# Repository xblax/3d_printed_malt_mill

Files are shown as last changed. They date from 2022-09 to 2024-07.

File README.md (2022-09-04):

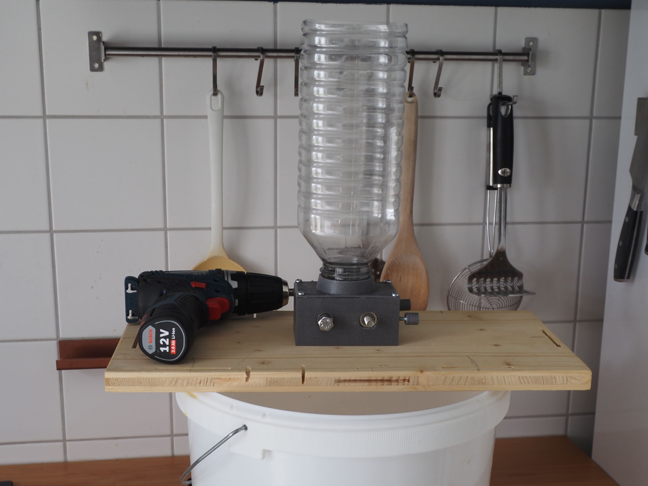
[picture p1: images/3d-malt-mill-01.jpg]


# 3D Printed Malt Mill

This is an open source malt mill design intended mainly for homebrewers with ~20 l batches and ~5 kg grain bills. The mill was designed to only use parts that are  available in many hardware stores to allow easy DIY reproduction and to keep the overall cost low.

For now, this design should still be considered as a work in progress - there is no long term experience for it's durability yet. To get a first impression you can check the photos in the [images](images) folder.

## Main Features

* Geared 40x40 mm rollers with ball bearings
* Adjustable gap (0.25 mm - 2.75 mm gap size)
* Separate hopper attachment part (currently one design for Bericap 48-41 threads)
* Powered by cordless screwdriver

## Bill of materials

Besides food safe PETG or PLA filament you need:

| Pieces | Part | Purpose
| --- | :--- | :---
| 2 | M8 x 80 mm fully threaded hex bolt | Axles
| 5 | M8 hex nut | Roller and gear insert nuts
| 4 | 608 ZZ bearing | Roller bearings
| 2 | M4 hex bolt | Adjustment screws
| 2 | M4 hex nut | Adjustment screw inserts
| 4 | 3x15 mm screws (spax or similiar) | Hopper attachment
| 4-6 | 3 mm screws (20 mm + board thickness) | Board attachment
| 1 | Bericap 48-41 threaded bottle | Hopper

Buying recommendations for Germans:  
All metal parts including the bearings should be cheaply available at Hornbach hardware store.
Bericap 48-41 threaded bottles are sold with 2-5 l distilled water in in many stores (i.e. DM, Edeka -- effective 2022).

## Printing considerations

Parts are intended to be printed with 0.25mm layer hight. The model pictured above was printed with PETG.

| Pieces | Part | File
| --- | :--- | :---
| 1 | Main mill frame | [frame.stl](stl/frame.stl)
| 2 | Roller | [roller.stl](stl/roller.stl)
| 2 | Gear | [gear.stl](stl/gear.stl)
| 2 | Adjustment knob | [knob.stl](stl/knob.stl)
| 1 | Spacer | [spacer.stl](stl/spacer.stl)
| 1 | Hopper attachment | [attachment\_bericap\_4841.stl](stl/attachment_bericap_4841.stl)

It's recommended to print the test parts in [stl/testparts](stl/testparts) first to test fitting of the parts and settings of your 3D printer.

#### Frame
Should be printed upside down. 2 perimeters, 3 top/bottom layers, 12-15% rectilinear infill should be sufficient. No support required.

#### Rollers

Should be printed in direction as rendered. Auto-generated support is required for the bottom nut insert. The lower nut insert is designed a bit deeper than the upper one to counter sagging of the top layers when printing.

Recommended settings are 3 perimeters and 15% rectilinear support. Consider to increase infill, perimeters or to add some solid layers for the first and last 6mm to improve strength of the nut inserts.

#### Gears

Should be printed with flat side down. Auto generated support for nut insert required. 3 perimeters, 3 top/bottom solid layers, 15% rectilinear infill.

## Assembly

All parts are press-fit or screwed together. The mill should be attached to a base board, screwed from the bottom.

## Source Files

Most parts were designed with Open Scad 2021.01. Exception are the gears which were created with FreeCad 0.19.

## License

This project is licensed under GPL v3. 

If you distribute STLs or prints based on this design you are require to provide the (changed) source files along with a copy of the GPL v3 license.

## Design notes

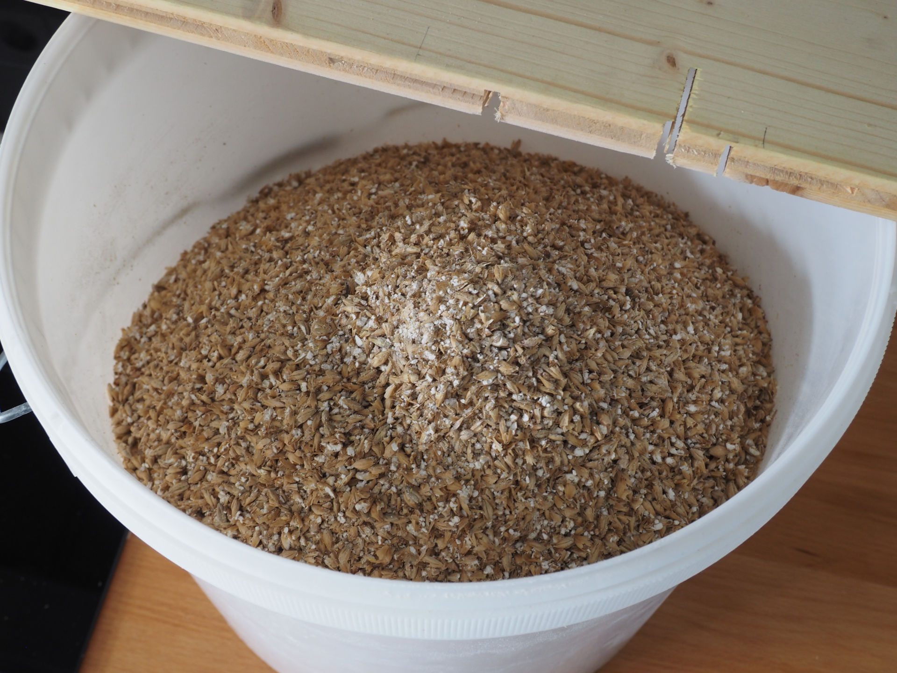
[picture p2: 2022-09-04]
images/3d-malt-mill-03.jpg

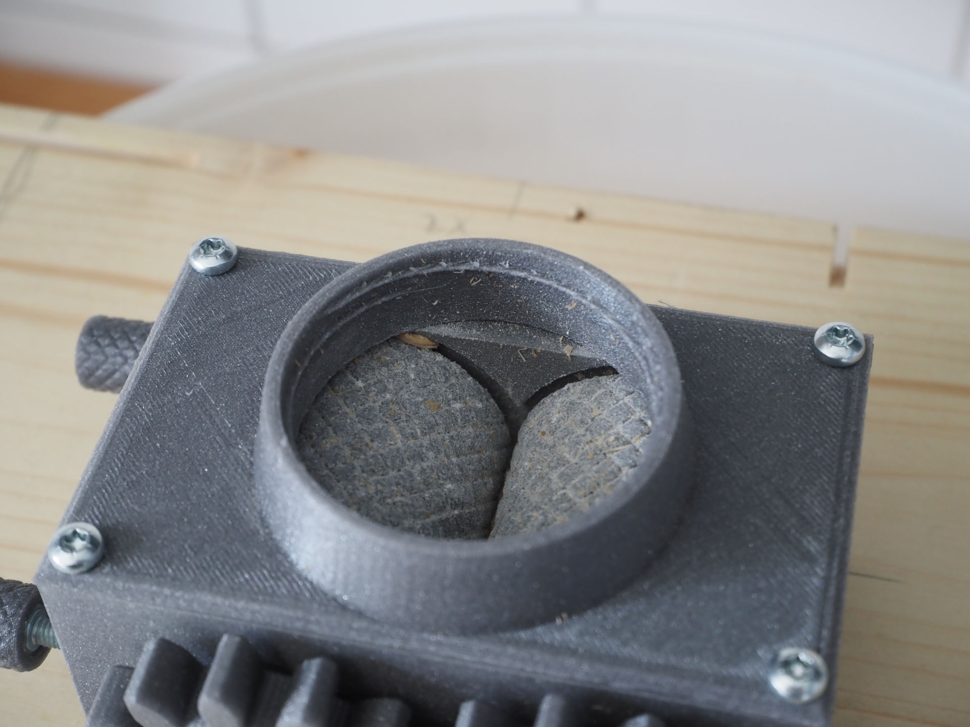
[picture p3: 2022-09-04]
images/3d-malt-mill-02.jpg

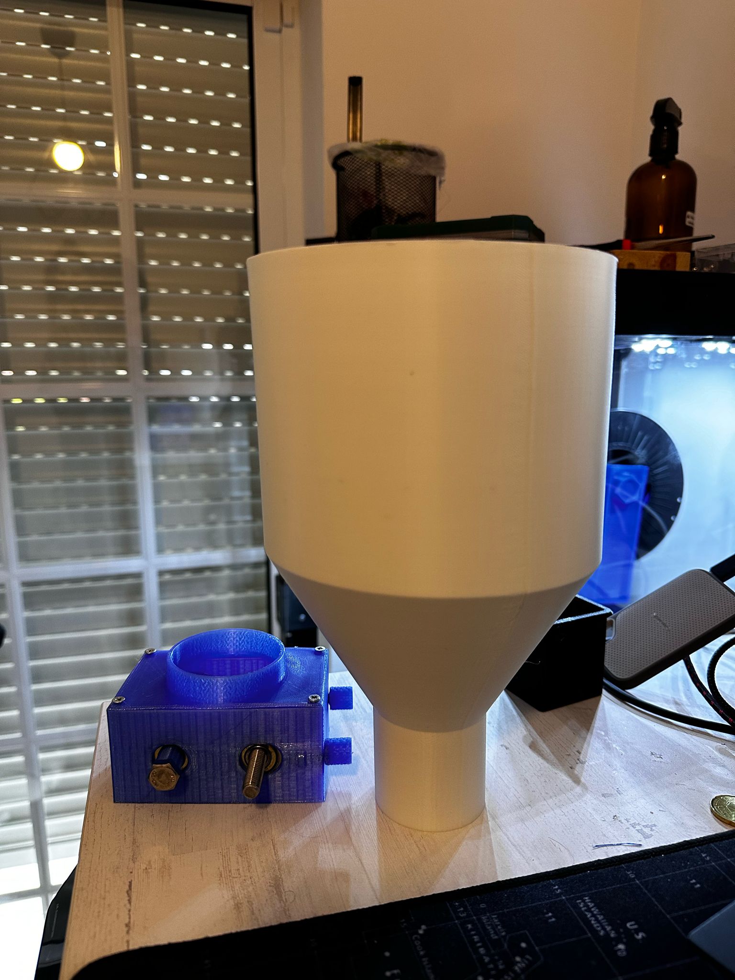
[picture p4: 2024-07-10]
images/funnel and attachment.jpg

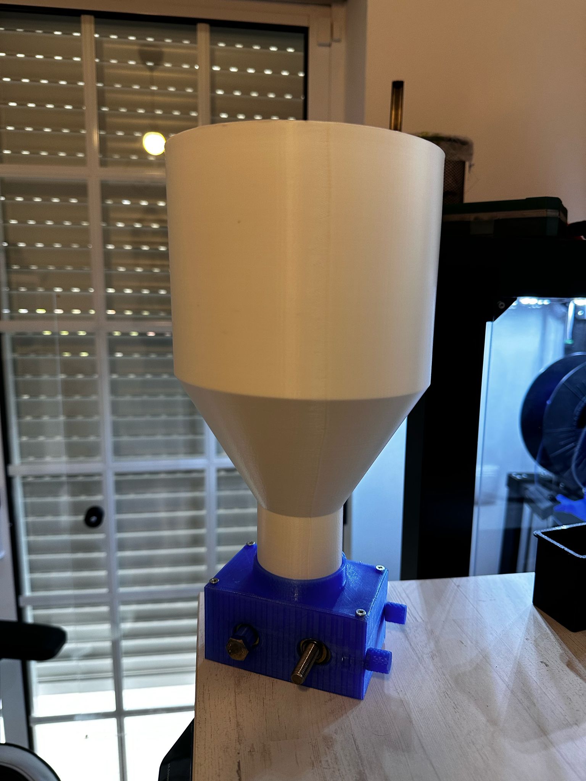
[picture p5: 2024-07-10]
images/funnel and lid.jpg

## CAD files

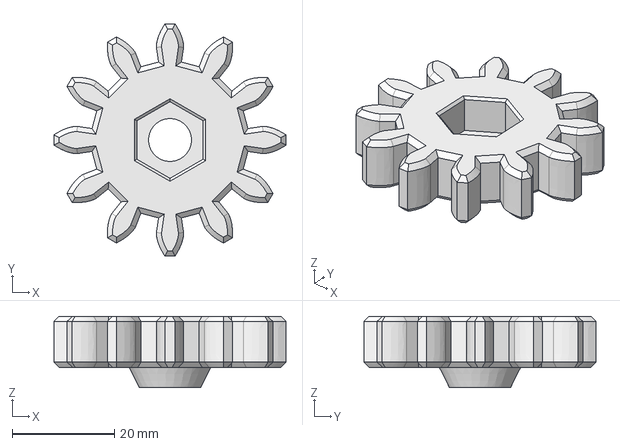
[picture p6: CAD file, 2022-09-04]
src/gear.FCStd
45.5 x 45.5 x 14.0 mm

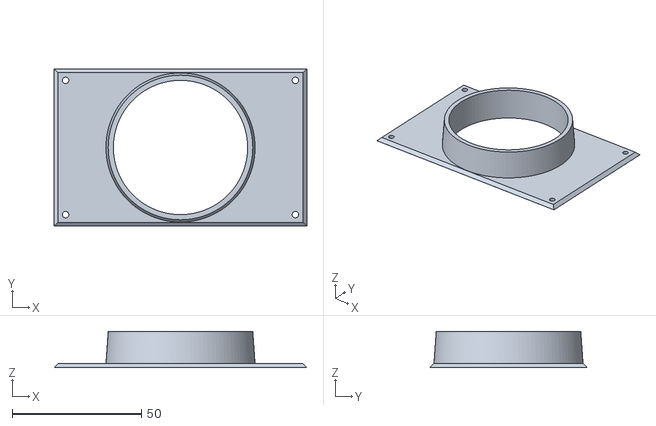
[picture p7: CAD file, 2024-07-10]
stl/attachment_no_thread.stl
98.0 x 61.0 x 14.0

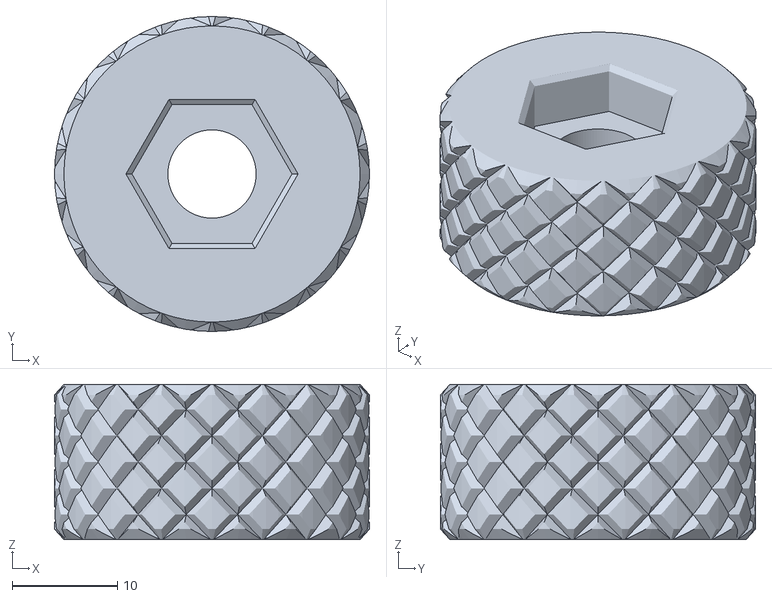
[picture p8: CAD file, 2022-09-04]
stl/testparts/test_roller.stl
30.0 x 30.0 x 14.8

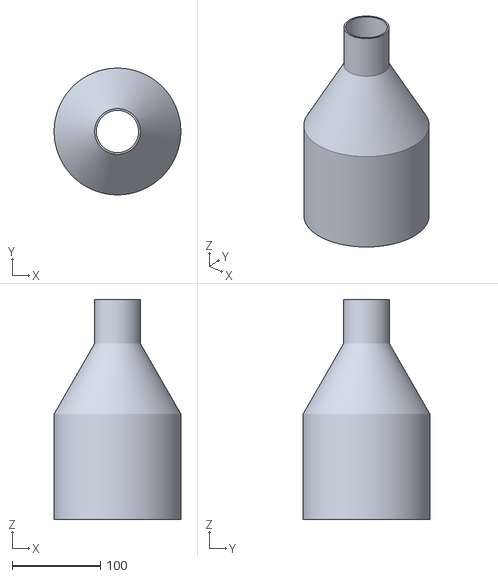
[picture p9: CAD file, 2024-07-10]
stl/funnel_no_thread.stl
144.0 x 144.0 x 250.0

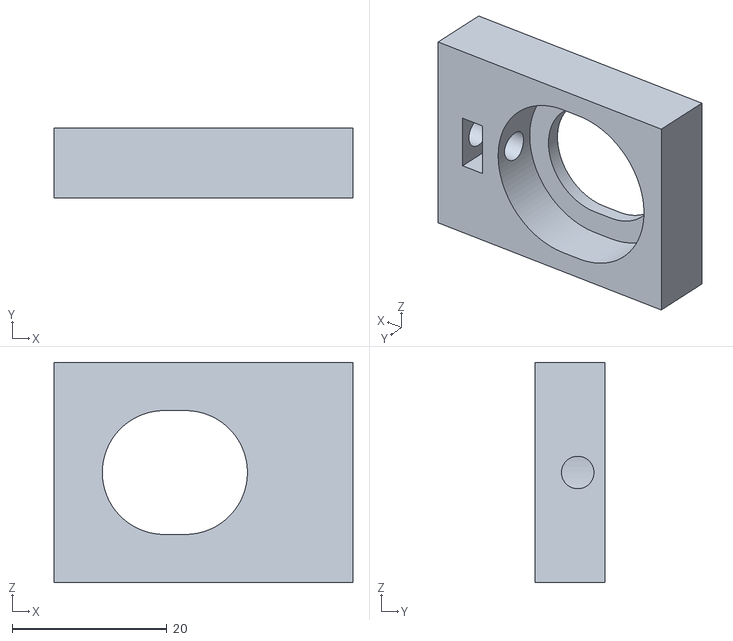
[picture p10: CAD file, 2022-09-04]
stl/testparts/test_frame.stl
38.6 x 9.00 x 28.5

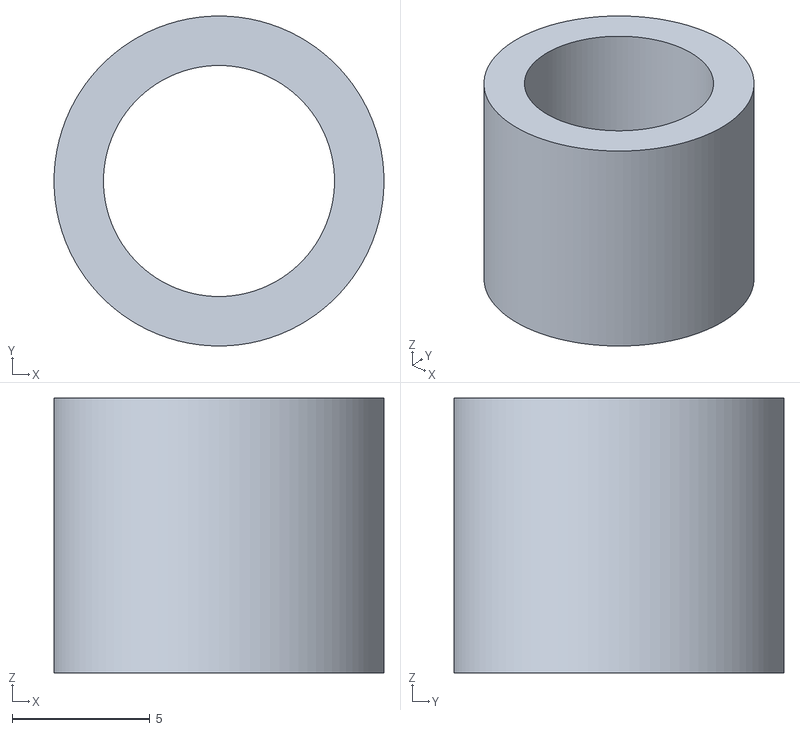
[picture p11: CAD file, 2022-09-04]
stl/spacer.stl
12.0 x 12.0 x 10.0

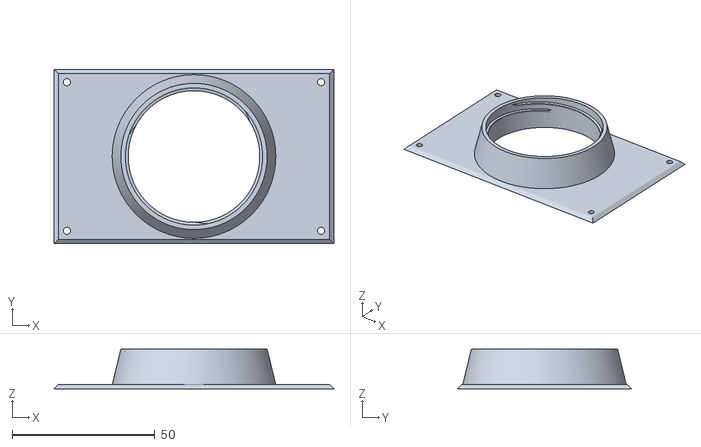
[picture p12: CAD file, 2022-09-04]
stl/attachment_bericap_4841.stl
98.0 x 61.0 x 14.0

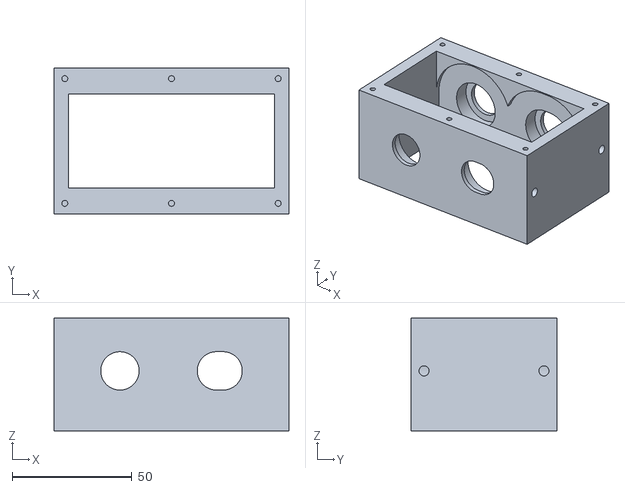
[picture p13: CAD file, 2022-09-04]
stl/frame.stl
98.0 x 61.0 x 47.0

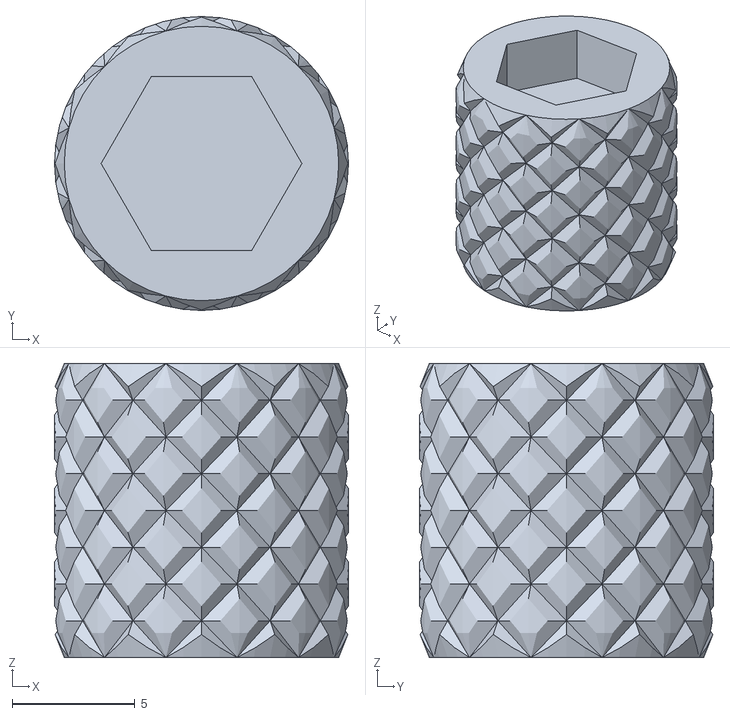
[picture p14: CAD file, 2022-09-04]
stl/knob.stl
12.0 x 12.0 x 12.0

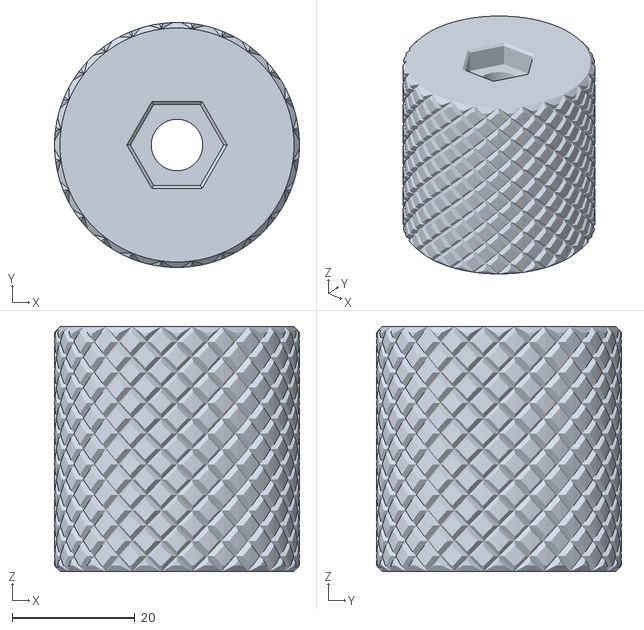
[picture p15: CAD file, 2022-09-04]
stl/roller.stl
40.0 x 40.0 x 40.0

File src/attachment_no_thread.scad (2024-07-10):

/* 
 * 3D Printed Malt Mill
 * Designed by xblax: https://github.com/xblax/3d_printed_malt_mill
 * Licensed GPL v3 
 */

use <knurledFinishLib_v2_1.scad>
use <thread_profile.scad>

$fn=100;
$eps=0.01;

// roller dimensions
$roller_width=40;
$roller_diameter=40;
$roller_min_dist=0.25;   // minimum distance between the two rollers
$roller_adj_range=2.75; // adjustable range of second roller

$roller_side_clearance=1.5;
$roller_head_clearance=1.5;
$roller_top_clearance=1.5;
$roller_bottom_clearance=5; // note: 5mm needed due to gear size

// frame walls
$frame_head_width=9; // thick enough for 7mm bearing inset
$frame_side_width=6;
$frame_top_width=0.5;

// calculated values
$frame_inner_width=$roller_diameter*2+$roller_side_clearance*2+$roller_min_dist+$roller_adj_range;
$frame_inner_depth=$roller_width+$roller_head_clearance*2;
$frame_inner_height=$roller_diameter+$roller_bottom_clearance+$roller_top_clearance;

$frame_width=$frame_inner_width+$frame_side_width*2;
$frame_height=$frame_inner_height+$frame_top_width;
$frame_depth=$frame_inner_depth+$frame_head_width*2;

$primary_roller_x=$frame_side_width+$roller_side_clearance+$roller_diameter/2;
$secondary_roller_x=$frame_side_width+$roller_side_clearance+$roller_diameter/2*3+$roller_min_dist;
$roller_z=$roller_bottom_clearance+$roller_diameter/2;

// mouting holes
$mounting_hole_diameter = 2.5; // to be used with 3mm screws
$mounting_hole_depth = 20; // should not collide with adjusment mechanism
$mounting_hole_inset = $frame_head_width/2;
$attachment_hole_depth = 15;


// top opening of frame
$top_opening_roller_overlap=2;
$top_opening_width=$frame_inner_width;
$top_opening_depth=$frame_inner_depth - 2 * $top_opening_roller_overlap;

// roller knurling
$knurl_wd=5;
$knurl_hg=5;
$knurl_dp=3;
$knurl_e_smooth=1;
$knurl_s_smooth=70;
$knurl_cylinder_od=$roller_diameter-($knurl_dp*(100-$knurl_s_smooth)/100); // calculate cylinder diameter (total diamater minus knurling)

// roller M8 axis parameters
$roller_axis_through_hole=8.4;
$insert_nut_size=13.2;
$insert_nut_thickness=6.25;
$insert_nut_clearance=0.15; // clearance between nuts and bearings - 0.3mm in total
$insert_nut_inset_bottom_adjust=0.5; // bottom side of the roller needs 0.5mm additional inset for the nut to due sagging of top layers when printed with support
$insert_nut_inset=$insert_nut_thickness - $roller_side_clearance + $insert_nut_clearance;
$insert_nut_outset=$insert_nut_thickness - $insert_nut_inset;
$insert_nut_chamfer=0.5;
$square_nut = false;

// paramters for 608Z bearings
$bearing_hole_diameter = 16;
$bearing_inset_depth = 7;
$bearing_inset_diameter = 22.5;

// adjustment mechanism: M4 parameters
$adj_screw_diameter=4.2;
$adj_nut_size=7.5;
$adj_nut_thickness=3.4;
$adj_nut_space=4;

// adjustment mechanism: knob parameters
$knob_height = 12;
$knob_width = 12;
$knob_nut_size=7.1;
$knob_nut_inset=3;

$knob_knurl_wd=3;
$knob_knurl_hg=3;
$knob_knurl_dp=1;
$knob_knurl_e_smooth=1;
$knob_knurl_s_smooth=60;
$knob_knurl_od=$knob_width-($knob_knurl_dp*(100-$knob_knurl_s_smooth)/100);

// attachment plate
$attachment_base_width = $frame_width;
$attachment_base_depth = $frame_depth;
$attachment_base_thickness = 1.5;
$attachment_wall_thickness=1.6;

// test object parameters
$test_roller_diameter=30;
$test_roller_width=$insert_nut_inset*2+5;
$test_knurl_cylinder_od=$test_roller_diameter-($knurl_dp*(100-$knurl_s_smooth)/100);

echo(str("Frame dimensions: ", $frame_width, " x ", $frame_depth, " x ", $frame_height));
echo(str("Cutout dimensions: ", $frame_inner_width, " x ", $frame_inner_depth));
echo(str("Mouting screws: ", ($frame_inner_width+$frame_head_width), " x ", ($frame_inner_depth+$frame_head_width), " (outset from cutout ", $frame_head_width/2, "mm)"));
//echo(str("Roller Distance ", $secondary_roller_x-$primary_roller_x, " + ", $roller_adj_range));
//echo(str("Roller Nut Outset ", $insert_nut_outset));

module nut(size, height)
{
    if( $square_nut )
    {  
        // square nut
        cube([size,size,height],center=true);
    }
    else
    {
        // hex nut
        cylinder($fn=6, d=size/cos(30), h=height, center=true);  
    }
}

module insert_nut_chamfer()
{
    hull()
    {
        translate([0,0,$insert_nut_chamfer])
        nut($insert_nut_size,$eps);
        nut($insert_nut_size+2*$insert_nut_chamfer, $eps);
    }
}

module roller_top_nut_insert(roller_width=$roller_width)
{
    translate([0,0,roller_width-$insert_nut_inset+$insert_nut_thickness/2])
    nut($insert_nut_size,$insert_nut_thickness);
    translate([0,0,roller_width])
    rotate([180,0,0])
    insert_nut_chamfer();
}

module roller_bottom_nut_insert()
{
    translate([0,0,($insert_nut_inset+$insert_nut_inset_bottom_adjust)-$insert_nut_thickness/2])
    nut($insert_nut_size,$insert_nut_thickness);
    insert_nut_chamfer();
}

/* Roller part for the malt mill (required twice) */
module roller()
{
    difference()
    {
        // Knurled cylinder
        knurl(k_cyl_hg= $roller_width, k_cyl_od = $knurl_cylinder_od, knurl_wd=$knurl_wd, knurl_hg=$knurl_hg, knurl_dp=$knurl_dp, e_smooth = $knurl_e_smooth, s_smooth=$knurl_s_smooth);

        // axis trough hole
        translate([0,0,-$eps])
        cylinder(d=$roller_axis_through_hole, h = $roller_width+1, $fn=100);
        // Top nut insert
        roller_top_nut_insert();
        // Bottom nut insert 
        roller_bottom_nut_insert();
    }
}

module base_frame()
{
    difference()
    {
        cube([$frame_width,$frame_depth,$frame_inner_height]);
        translate([$frame_side_width,$frame_head_width,-$eps])
        cube([$frame_inner_width,$frame_inner_depth,$frame_inner_height+2*$eps]);  
    }
}

module axis_through_hole(xpos,zpos=$roller_z)
{
    translate([xpos,-$eps,zpos])
    rotate([-90,0,0])
    cylinder(h=$frame_depth+2*$eps,d=$bearing_hole_diameter);
}

module bearing_cylinder(xpos,zpos=$roller_z)
{
    bearing_cylinder_length=$frame_inner_depth+2*$bearing_inset_depth;
    bearing_cylinder_y=$frame_head_width-$bearing_inset_depth;  
    translate([xpos,bearing_cylinder_y,zpos])
    rotate([-90,0,0])
    cylinder(h=bearing_cylinder_length,d=$bearing_inset_diameter);
}

module adj_through_hole(ypos, zpos=$roller_z, roller_pos=$secondary_roller_x,
frame_width=$frame_width)
{
    translate([frame_width+$eps,ypos,zpos])
    rotate([0,-90,0])
    cylinder(d=$adj_screw_diameter,h=frame_width-roller_pos);
}

module adj_nut_cutout(zpos=$roller_z, roller_pos=$secondary_roller_x+$adj_nut_space)
{
    translate([roller_pos+$roller_adj_range+$bearing_inset_diameter/2,
    -$adj_nut_size/2+$frame_head_width-($bearing_inset_depth)/2,-$adj_nut_size/2+zpos])
    cube([$adj_nut_thickness,$adj_nut_size*2+$frame_inner_depth,$adj_nut_size]);   
}

module mounting_hole(x,y)
{
    translate([x,y,$mounting_hole_depth/2-$eps])
    cylinder(d=$mounting_hole_diameter,h=$mounting_hole_depth, center=true);
}

module attachment_hole(x,y)
{
    translate([x,y,$frame_inner_height+$frame_top_width-15/2+$eps])
    cylinder(d=2.5,h=15, center=true);
}

module chamfered_cylinder(d, h, chamfer_x, chamfer_z)
{
    cylinder(d1=d-2*chamfer_x, d2=d,h=chamfer_z+$eps);
    translate([0,0,chamfer_z])
    cylinder(d=d, h=h-2*chamfer_z+$eps);
    translate([0,0,h-chamfer_z])
    cylinder(d2=d-2*chamfer_x, d1=d,h=chamfer_z);
}

/* Main frame part for the malt mill */
module frame()
{
difference()
{
    // frame without attachment / mounting cutouts
    union()
    {  
        // base frame with cutouts
        difference()
        {
            base_frame();

            // cutouts for primary roller
            axis_through_hole(xpos=$primary_roller_x);
            bearing_cylinder(xpos=$primary_roller_x);

            // cutouts for secondary roller
            hull()
            {
                // through hole secondary roller min_adj
                axis_through_hole(xpos=$secondary_roller_x);
                // throuh hole sceondary roller max_adj
                axis_through_hole(xpos=$secondary_roller_x+$roller_adj_range);
            }
            hull()
            {
                // through hole secondary roller min_adj
                bearing_cylinder(xpos=$secondary_roller_x);
                // throuh hole sceondary roller max_adj
                bearing_cylinder(xpos=$secondary_roller_x+$roller_adj_range);
            }

            // adj through hole front
            adj_through_hole(ypos=$frame_head_width-($bearing_inset_depth)/2);
            // adj through hole back
            adj_through_hole(ypos=$frame_head_width+$frame_inner_depth+($bearing_inset_depth)/2);
            // adj nut cutout
            adj_nut_cutout();
        }
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

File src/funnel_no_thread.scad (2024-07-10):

$fa=0.5; // default minimum facet angle is now 0.5
$fs=0.5; // default minimum facet size is now 0.5 mm

// Parametric Funnel by Coasterman

// VARIABLES
bottom_diameter = 140;
bottom_height = 120;
top_diameter = 48;
top_height = 50;
width = 2.0;
cone_height = 80;

// CODE
union()
{
difference()
{
cylinder(h=bottom_height, r=bottom_diameter/2 + width);
translate([0,0,-2]) cylinder(h=bottom_height+4, r=bottom_diameter/2);
}
translate([0, 0, bottom_height])
difference()
{
cylinder(h=cone_height, r1=bottom_diameter/2 + width, r2 = top_diameter/2 + width);
translate([0,0,0]) cylinder(h=cone_height, r1=bottom_diameter/2, r2 = top_diameter/2);
}
translate([0, 0, cone_height + bottom_height])
{
difference()
{
cylinder(h=top_height, r=top_diameter/2 + width);
translate([0,0,-2]) cylinder(h=top_height+4, r=top_diameter/2);
}
}
}

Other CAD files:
stl/gear.stl
src/mill.scad

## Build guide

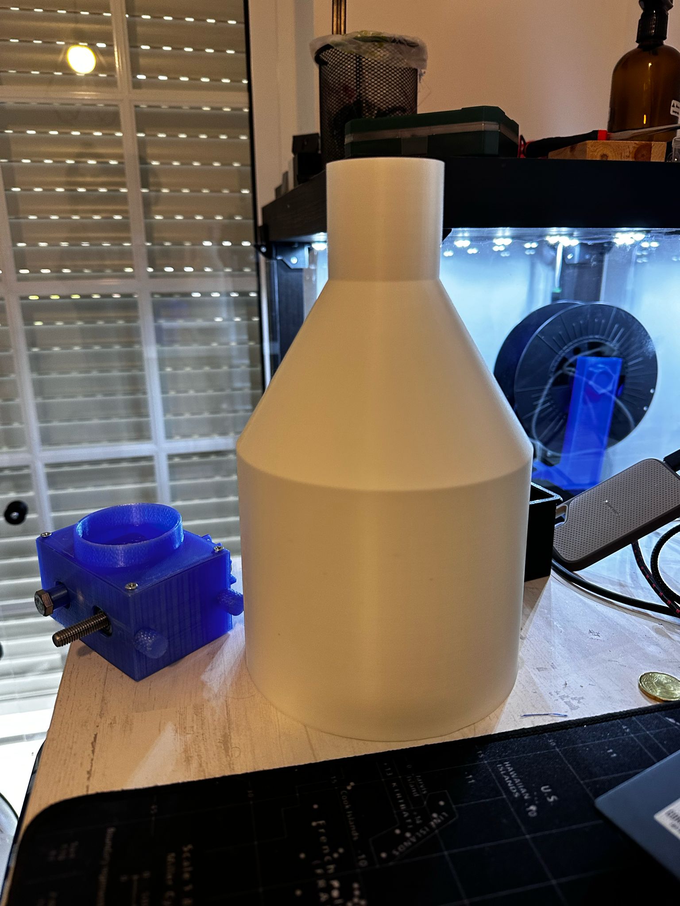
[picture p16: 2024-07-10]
images/funnel print orientation.jpg

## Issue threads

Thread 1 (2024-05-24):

HOW-TO mount

aamarques, 2024-05-24:
Could you provide more photos ? So we can see where the nuts were, the process of build, etc.

Thanks

xblax, 2024-05-26:
You can check out this thread in German home brewer forum via translator:
https://hobbybrauer.de/forum/viewtopic.php?t=29111&start=100
There are some more photos of this model and also some general chat about 3D printed malt mills and other options and ideas.

Closed 2024-07-10.

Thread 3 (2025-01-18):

metal parts assembly

jiyuwazadsgn, 2025-01-18:
Hi,

I printed your malt mill. Thanks for this, seems to be good stuff. Is it possible to have pictures of the metal parts assembly inside the malt mill ? Thanks a lot, have a great day.

Blaise

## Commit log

2022-09-04 Add initial version of the malt mill.
    [attachment_bericap_4841.stl, frame.stl, gear.FCStd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]
2024-05-27 This is a funnel in replace of Bericap 4841
    [funil_brew.scad]
2024-05-27 The Lid and Attachment
    The Lid and Attachment without threads to join the funnel
    [Attachement no thred.scad]
2024-05-27 STL Files
    [Lid_attachment-no-threds.stl, funil_no_threds.stl]
2024-07-10 Rename files for funnel and attachment without thread
    Contributed by @aamarques
    [attachment_no_thread.scad, attachment_no_thread.stl, funnel_no_thread.scad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]
